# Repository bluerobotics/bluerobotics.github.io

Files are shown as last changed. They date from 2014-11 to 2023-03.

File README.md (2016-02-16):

Blue Robotics Documentation Website 
===================================

This repository is the home to Blue Robotics' product documentation, including product manuals, tutorials, and guides. This information is licensed under the Creative Commons Attribution-ShareAlike 4.0 International License. We welcome and encourage contributions from others as well as reports of issues or errors.

For more information please visit the actual [documentation site](http://docs.bluerobotics.com/).

##How the Website Works

The documentation website uses the [Github Pages feature](https://pages.github.com/) to host the website directly from this repository. The documentation is written in [Markdown](https://help.github.com/articles/markdown-basics/) and uses [Jekyll](http://jekyllrb.com/) to generate the website.

If you want to play around with it and make modifications, just create a [fork of the repository](https://github.com/bluerobotics/bluerobotics.github.io/fork).

When you've got the files on your computer, you can host the site locally by typing:

```bash
jekyll serve
```

Then visit the site at http://localhost:4000/.

For more information on how to install Jekyll on your computer, visit the [Jekyll website](http://jekyllrb.com/).

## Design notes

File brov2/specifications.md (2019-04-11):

---
layout: default
title: BlueROV2
permalink: /brov2/
order: 1
topnavbar: brov2
nav:
- Introduction: introduction
- - Features: features
- - What's Included: whats-included
- - What's Not Included: whats-not-included
- - Resources
- Specifications: specifications
- - Physical: physical
- - Performance: performance
- - Battery: battery
- - Lights: lights
- - Tether: tether
- - Sensors: sensors
- - Camera Tilt: camera-tilt
- - Camera: camera
- 2D Drawing: 2d-drawing
- 3D Model: 3d-model
- User Manuals: user-manuals
- Issue Reporting: issue-reporting

store-links:
- BlueROV2: https://www.bluerobotics.com/store/rov/bluerov2/

manual-links:
- Assembly Manual: /brov2/assembly/
- Software Setup: /brov2/software-setup/
- Operation Manual: /brov2/operation/

redirect: https://bluerobotics.com/store/rov/bluerov2/bluerov2/#tab-technical-details
---

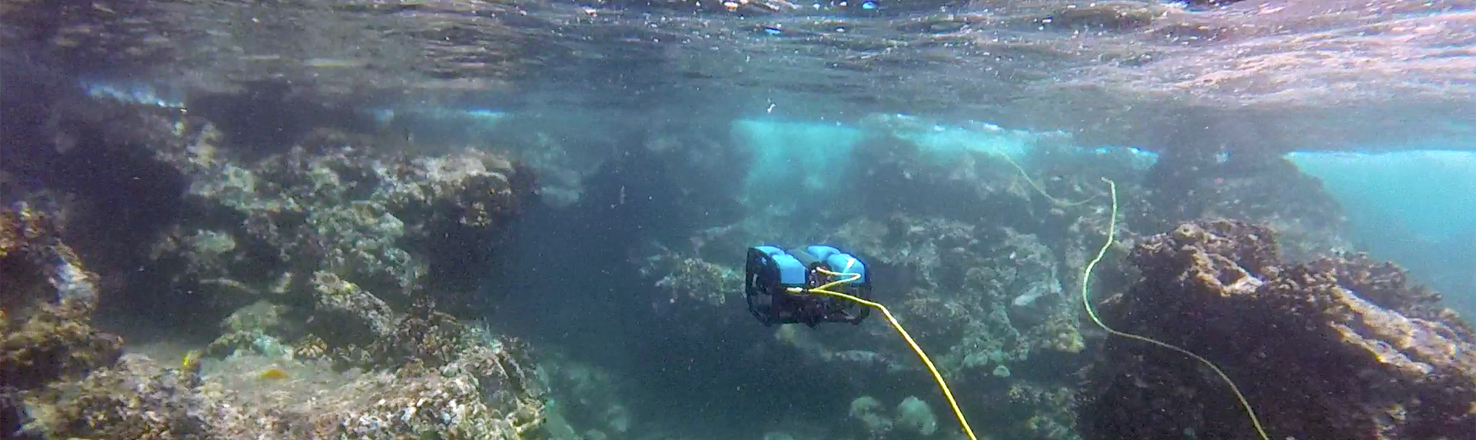
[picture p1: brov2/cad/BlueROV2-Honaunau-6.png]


# Introduction

The _BlueROV2_ is the world's most affordable high-performance ROV. The 6-thruster vectored configuration, coupled with strong static stability, provides a vehicle that is smooth and stable, yet highly maneuverable. The _BlueROV2_ provides the capabilities of a 
high-end commercial mini-ROV at the price of the most basic commercial ROVs.

<a href="http://bluerobotics.com/downloads/bluerov2.pdf" alt="BlueROV2 Datasheet"><i class="fa fa-download" aria-hidden="true"></i> Download Datasheet</a>

## Features

- Live 1080p HD video
- Highly maneuverable vectored thruster configuration
- Stable and optimized for inspection- and research-class missions
- Easy to use, cross-platform user interface
- Highly expandable with three free cable penetrators
- Standard 100m depth rating and up to 300m tether available
- 6 T200 Thrusters and Basic ESCs for the best thrust-to-weight ratio in its class
- Battery powered with quick-swappable batteries for long missions

## What's Included

The kit arrives almost-ready-to-dive with pre-built subassemblies. The expected build time is 1.5-3 hours to operation depending on experience.

You can find the full bill of materials for the for the _BlueROV2_ kit on the [store page](http://www.bluerov2.com/).

## What's Not Included

There are some items necessary for operation that are not included with the kit. 

 - A gamepad controller. We recommend [this XBox One Controller](https://www.microsoft.com/en-us/store/d/xbox-wireless-controller/8vcw8gln9vrf/ljvk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) or [this Logitech Gamepad](http://gaming.logitech.com/en-us/product/f310-gamepad).
 - A laptop or a Windows 10 tablet. QGroundControl works on Mac, Windows 10, and Linux.
 - A battery for the BlueROV2. We recommend getting our [18Ah Lithium-ion Battery](https://www.bluerobotics.com/store/rov/bluerov2/battery-li-4s-18ah-r2-rp/) or 2 or 3 of [these](https://hobbyking.com/en_us/multistar-high-capacity-10000mah-4s-12c-multi-rotor-lipo-pack-w-xt90.html)
 - A battery charger, such as our [Lithium Battery Charger](http://www.bluerobotics.com/store/electronics/batteries/lithium-battery-charger/).  

## Resources

 - [Assembly Instructions](/brov2/assembly/)
 - [Bill of Materials](http://www.bluerov2.com) (see Contents tab)
 - [Initial Software Setup](/brov2/software-setup)
 - [Operating Manual](/brov2/operation)

# Specifications

## Physical 

| Length                                 | 457 mm                     | 18 in                      |
| Width                                  | 338 mm                     | 13.3 in                    |
| Height                                 | 254 mm                     | 10 in                      |
| Weight in Air (with Ballast)           | 10-11 kg                   | 22-24 lb                   |
| Weight in Air (without Ballast)        | 9-10 kg                    | 20-22 lb                   |
| Net Buoyancy (with Ballast)            | 0.2 kg                     | 0.5 lb                     |
| Net Buoyancy (without Ballast)         | 1.4 kg                     | 3 lb                	   |
| Watertight Enclosure Inner Diameter    | 102 mm                     | 4.0 in                     |
| Watertight Enclosure Inner Length      | 298 mm                     | 11.75 in                   |
| Cable Penetrator Holes                 | 14 x 10mm                  | 14 x 0.4 in                |
| Construction                           | HDPE frame, aluminum flanges/end cap, and acrylic tubes |
| Main Tube (Electronics Enclosure)      | [Blue Robotics 4 inch series w/ aluminum end caps](http://docs.bluerobotics.com/watertight-enclosures/#specifications-4-series)        |
| Battery Tube                           | [Blue Robotics 3 inch series w/ aluminum end caps](http://docs.bluerobotics.com/watertight-enclosures/#specifications-3-series)        |
| Buoyancy Foam                          | [R-3318 Urethane Foam](https://www.bluerobotics.com/store/buoyancy-ballast/float-r3318-r1/) rated to 244 meters                |
| Ballast Weight                         | 6 x [200 g coated lead weights](https://www.bluerobotics.com/store/parts/ballast-200g-r1/)                             |
| Battery Connector						 | XT90                                                    |

## Performance 

| Maximum Rated Depth                    | 100 m         | 330 ft        |
| Maximum Tested Depth (so far)          | 130 m         | 425 ft        |
| Maximum Forward Speed                  | 1 m/s         | 2 knots       |
| Thrusters                              | [Blue Robotics T200](http://docs.bluerobotics.com/thrusters/t200/)            |
| ESC                                    | [Blue Robotics Basic 30A ESC](http://docs.bluerobotics.com/besc/)   |
| Thruster Configuration                 | [6 thrusters](http://ardusub.com/images/vectored-frame.png)                   |
|                                        | - 4 Vectored                  | 
|                                        | - 2 Vertical                  | 
| Forward Bollard Thrust (45°)           | 9 kg<sub>f</sub>      | 19.8 lb<sub>f</sub>     |
| Vertical Bollard Thrust                | 7 kg<sub>f</sub>       | 15.4 lb<sub>f</sub>      |
| Lateral Bollard Thrust (45°)           | 9 kg<sub>f</sub>      | 19.8 lb<sub>f</sub>      |

## Battery

| Battery Life (Normal Use)              | ~3 hours w/ [18AH Lithium-ion Battery](https://bluerobotics.com/store/rov/bluerov2/battery-li-4s-18ah-r2-rp/) |
| Battery Life (Light Use)               | ~5 hours w/ [18AH Lithium-ion Battery](https://bluerobotics.com/store/rov/bluerov2/battery-li-4s-18ah-r2-rp/) |

The batteries can be changed in about 30 seconds.

## Lights

| Brightness       | 1500 lumens each with dimming control                  |
| Light Beam Angle | 135 degrees, with adjustable tilt                    |

## Tether

| Diameter | 7.6 mm | 0.30 in |
| Length   | 25-300 m | 80-980 ft |
| Working Strength | 45 kg<sub>f</sub> | 100 lb<sub>f</sub> |
| Breaking Strength | 160 kg<sub>f</sub> | 350 lb<sub>f</sub> |
| Strength Member | Kevlar with waterblock |
| Buoyancy in Freshwater | Neutral |
| Buoyancy in Saltwater | Slightly Positive |
| Conductors | 4 twisted pairs, 26 AWG |

## Sensors

- 3-DOF Gyroscope (on the PixHawk)
- 3-DOF Accelerometer (on the PixHawk)
- 3-DOF Magnetometer (on the PixHawk)
- Internal barometer (on the PixHawk)
- [Blue Robotics Bar 30 Pressure/Depth and Temperature Sensor](http://docs.bluerobotics.com/bar30/) (external) 
- Current and Voltage Sensing (included with the PixHawk)

## Camera Tilt
					   
| Tilt Range                 | +/- 90 degree camera tilt (180 total range)                                             | 
| Tilt Servo                 | Hitec HS-5055MG         |

## Camera

| Field of View (Underwater) | 110 degrees (horizontal)                                                              |                                                      
| Light Sensitivity          | 0.01 [lux](https://en.wikipedia.org/wiki/Lux#Illuminance)                              |
| Resolution                 | 1080p                                                                                 |

## Control System

| Tether Interface Board              	| [Fathom-X Tether Interface Board](http://docs.bluerobotics.com/fathom-x/)                |
| Control System 						| [M Robotics PixHawk](https://www.bluerobotics.com/store/electronics/pixhawk-r1/)         |

# 2D Drawing

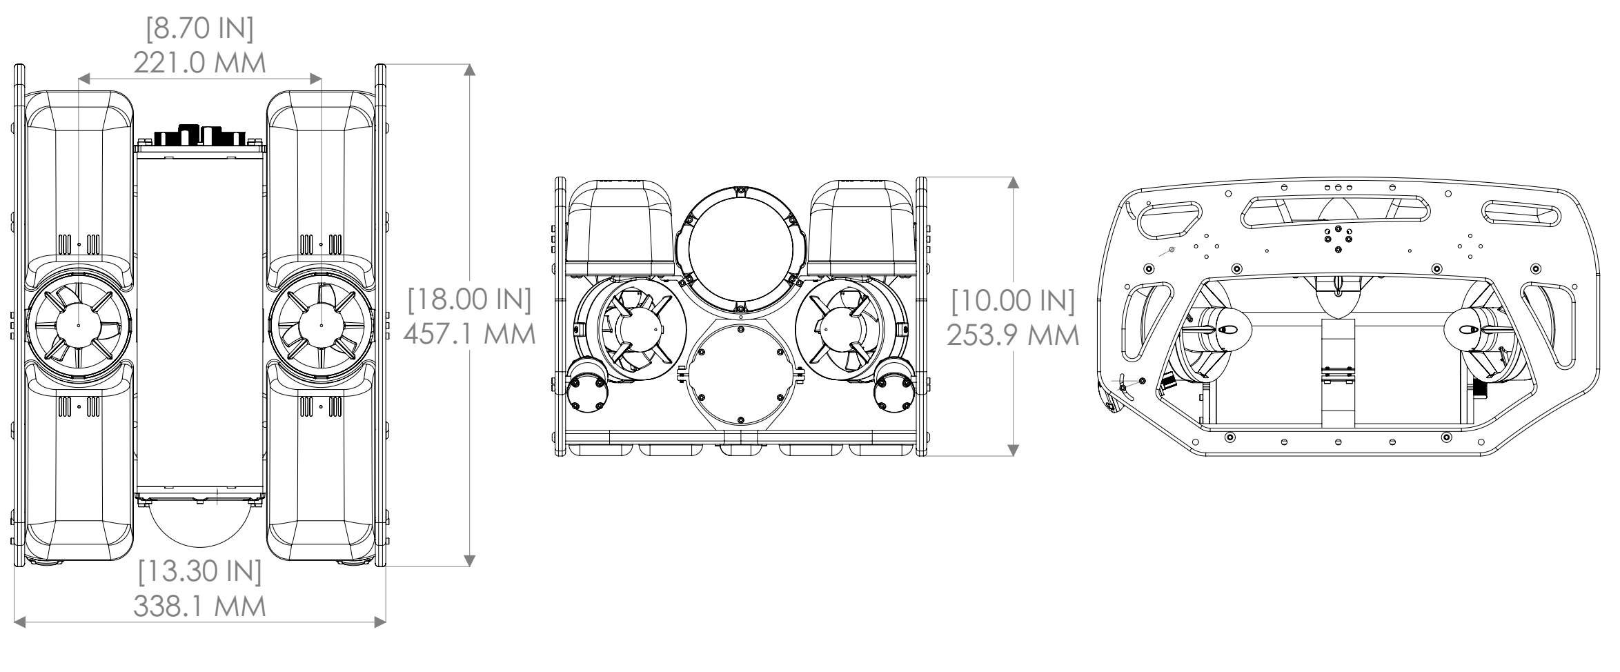
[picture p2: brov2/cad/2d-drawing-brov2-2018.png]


# 3D Model

These are BIG files since the model is fairly complex. If you just want to check out a 3D view or 3D models of the BlueROV, we recommend [checking out the CAD files on GrabCAD](https://grabcad.com/library/bluerobotics-bluerov2-standard-1).

# User Manuals

1. Please look at our [Assembly Manual](/brov2/assembly) for more detailed assembly instructions.

2. If you **received your BlueROV2 after October 24, 2016**, please look at our [Software Setup Manual](/brov2/software-setup/) for more details on setting up your topside computer. If you **received your BlueROV2 prior to October 24, 2016** please look at our [ArduSub Documentation](http://ardusub.com/introduction/#overview) for more details on the control software.

3. Please look at our [_BlueROV2_ Operating Manual](/brov2/operation) for a detailed operating manual.

# Issue Reporting

We're always trying to make our documentation, instructions, software, and user experience better. If you're having an issue with anything, please report it so that we can address it as soon as possible! Here's where to do that depending on what's wrong:

- **ArduSub Issues:** For anything related to the ArduSub software that runs on the Pixhawk and controls the ROV, reports issues on the [ArduSub Github Issues Page](https://github.com/bluerobotics/ardusub/issues). If you're unsure where your issue should be posted, you can report it here.
- **QGroundControl Issues:** For anything related to the QGroundControl software, joystick setup, video streaming, etc., please report an issue on the [QGroundControl Github Issues Page](https://github.com/mavlink/qgroundcontrol/issues).
- **Documentation:** For anything related to the documentation and instructions here, please report an issue on the [Blue Robotics Documentation Github Issues Page](https://github.com/bluerobotics/bluerobotics.github.io/issues).

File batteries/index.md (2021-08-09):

---
layout: default
title: Lithium-Ion Battery Documentation
permalink: /batteries/
order: 1
nav:
- Moved: this-page-has-been-moved

store-links:
- Lithium Battery Charger: http://www.bluerobotics.com/store/electronics/batteries/lithium-battery-charger/
- Lithium-ion Battery (14.8V, 18Ah):  https://www.bluerobotics.com/store/comm-control-power/batteries/battery-li-4s-18ah-r2-rp/
manual-links:
- BlueROV2: /brov2
- Lithium Battery Charger: /charger

redirect: https://bluerobotics.com/learn/battery-info/
---

# This Page Has Been Moved

We're in the process of reorganizing our documentation pages! Most product specifications, 2d drawings, and 3d models have been moved to their respective product pages.

**Please continue to the [Lithium-ion Battery store page on our website](https://www.bluerobotics.com/store/comm-control-power/batteries/battery-li-4s-18ah-r2-rp/) to find the most relevant charger info!**

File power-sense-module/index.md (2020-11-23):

---
layout: default
title: Power Sense Module
permalink: /power-sense-module/
order: 1
nav:
- Installation: installation
- - General: general
- - On the BlueROV2: on-the-bluerov2
- ArduSub Software Setup: ardusub-software-setup

store-links:
- Power Sense Module: https://www.bluerobotics.com/store/sensors-sonars-cameras/sensors/psm-asm-r2-rp-1/

manual-links:
- BlueROV2: /brov2

---

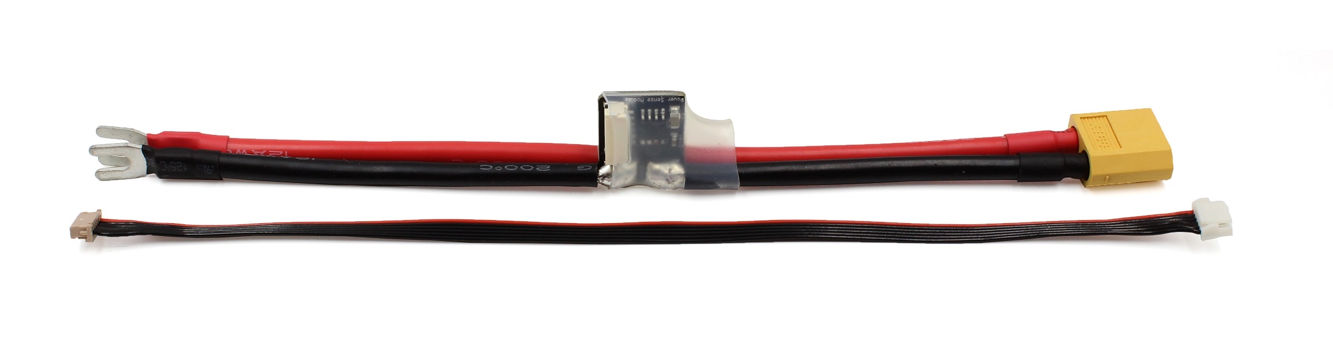
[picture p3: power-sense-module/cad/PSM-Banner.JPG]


# Installation

## General

1. Connect the wires with the attached spades to a power distribution board.
2. Connect the XT60 to a battery or power supply.
3. Connect the 6-position JST-GH to DF13 cable (GH plug side) into the the JST-GH socket on the Power Sense Module.
4. Connect the 6-position JST-GH to DF13 cable (DF13 plug side) into the DF13 POWER socket on the Pixhawk. 

## On the BlueROV2

### Step 1: Remove old Power Module

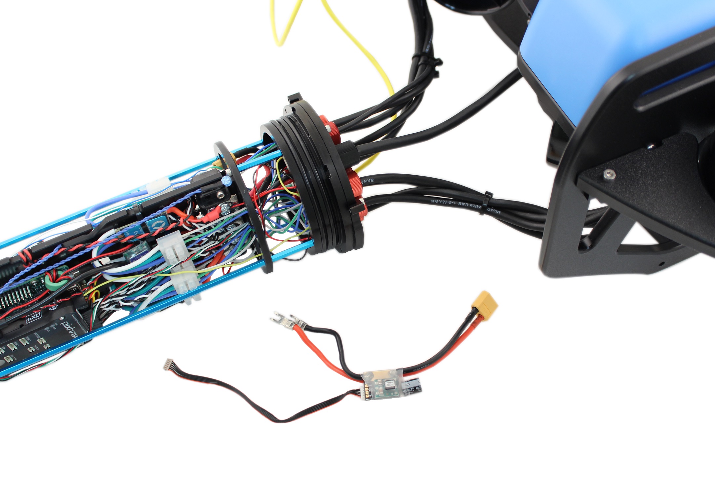
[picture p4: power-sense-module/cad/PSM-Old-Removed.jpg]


Disconnect the old Power Module spade connections (Positive and Negative) on the BlueROV2 terminal blocks. Disconnect the yellow XT60 connector. Depending on when you purchased your ROV, you may have a secondary XT60 connection that can also be disconnected. Disconnect the DF13 cable plug from the POWER port on the Pixhawk.

### Step 2: Connect the power spades

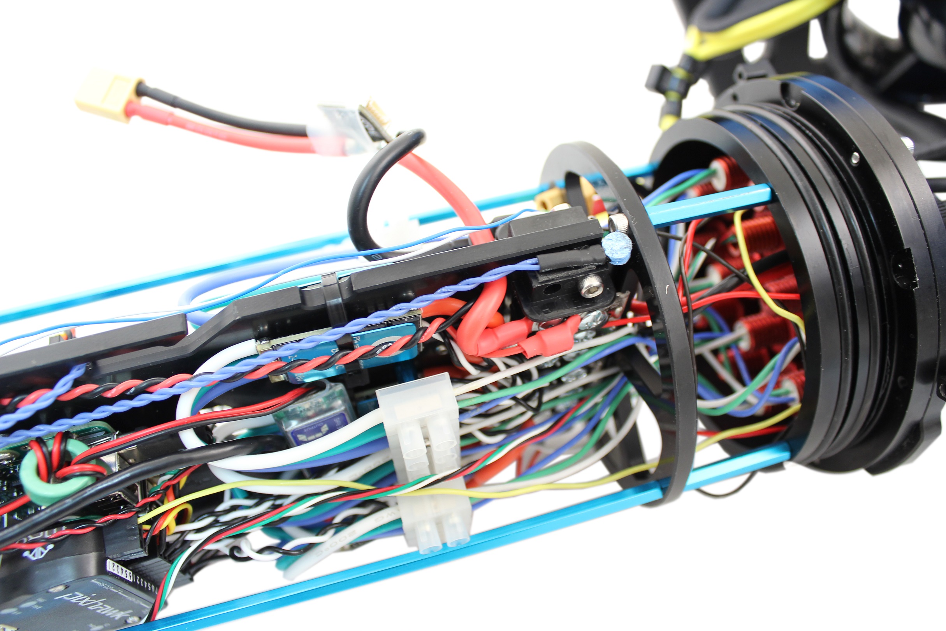
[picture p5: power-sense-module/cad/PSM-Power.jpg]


Connect the positive and negative power wire spades into their respective terminal blocks.

### Step 3: Connect the XT60

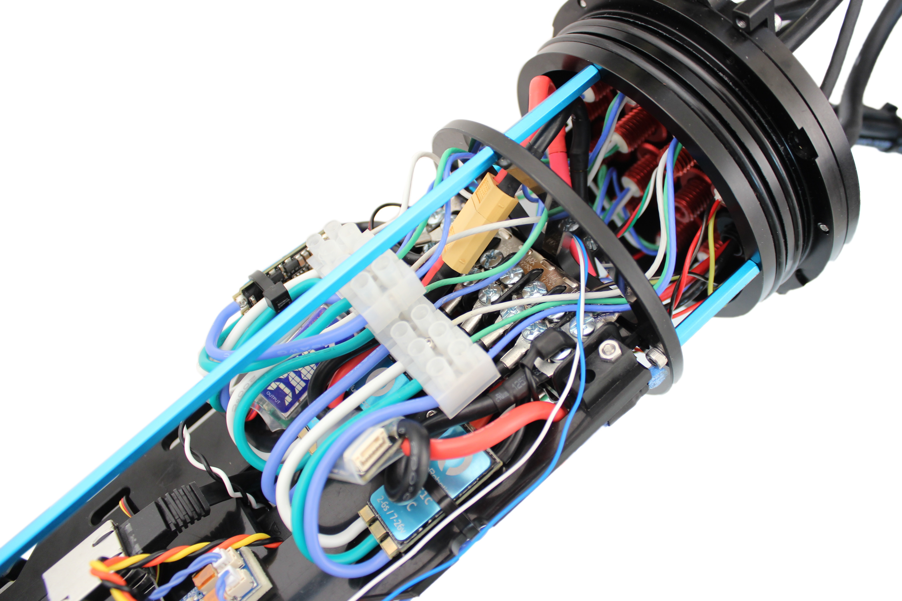
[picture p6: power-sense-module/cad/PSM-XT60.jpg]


Connect the yellow XT60 from the Power Sense Board to the XT60 power input coming from the endcap.

### Step 3: Connect the JST-GH to DF13 cable

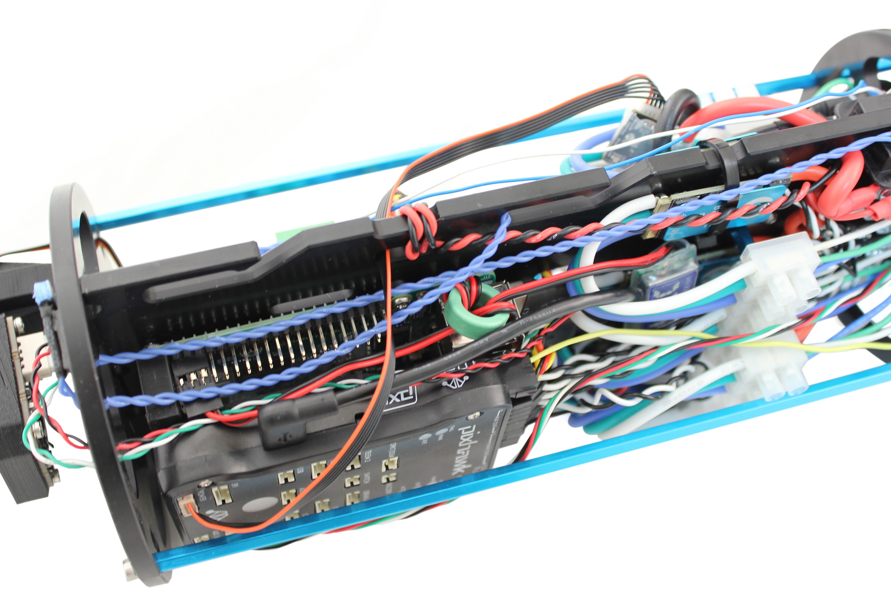
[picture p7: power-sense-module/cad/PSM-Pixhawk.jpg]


Connect the 6-position JST-GH to DF13 cable (GH plug side) into the the JST-GH socket on the <em>Power Sense Module</em>. Connect the JST-GH to DF13 cable (DF13 plug side) into the DF13 POWER socket on the Pixhawk.

# ArduSub Software Setup

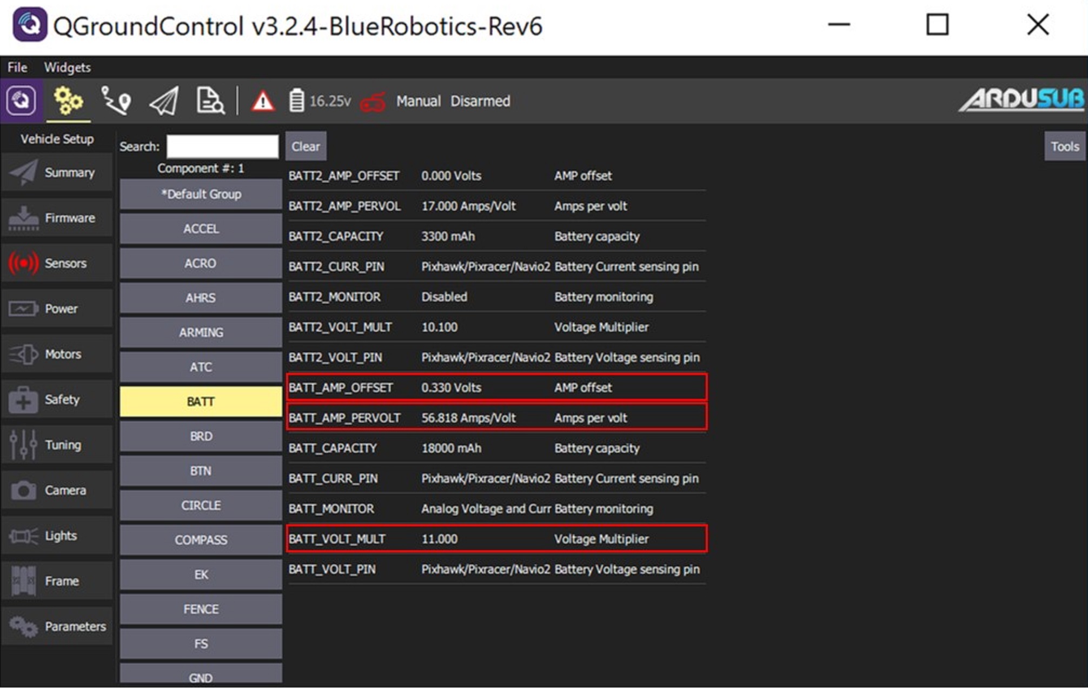
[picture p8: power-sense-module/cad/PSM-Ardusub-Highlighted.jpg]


If you have an R2 PSM (24 mm long):
In the Parameters tab of the QGroundControl Vehicle Setup page, select "BATT" and enter the following values:

| BATT_AMP_OFFSET | 0.330 | Amp Offset | 
| BATT_AMP_PERVOLT | 37.8788 | Amps per volt |
| BATT_VOLT_MULT | 11.000 | Voltage Multiplier |

If you have an R1 PSM (16 mm long):
In the Parameters tab of the QGroundControl Vehicle Setup page, select "BATT" and enter the following values:

| BATT_AMP_OFFSET | 0.330 | Amp Offset | 
| BATT_AMP_PERVOLT | 56.81818 | Amps per volt |
| BATT_VOLT_MULT | 11.000 | Voltage Multiplier |

If you have not already done so, ensure the following values are set:

| BATT_CAPACITY | 18000 | Battery capacity |
| BATT_CURR_PIN | Pixhawk | Battery Current sensing pin |
| BATT_MONITOR | Analog Voltage and Current | Battery monitoring |
| BATT_VOLT_PIN | Pixhawk | Battery Voltage sensing pin |

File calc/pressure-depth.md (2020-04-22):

---
layout: default
title: Pressure/Depth Calculator
permalink: /calc/pressure-depth/
canonical_url: https://bluerobotics.com/learn/pressure-depth-calculator/
order: 0
nav:
- Calculator: calculator
- Learn More: learn-more

redirect: https://bluerobotics.com/learn/pressure-depth-calculator/
---

# Calculator

This calculator determines the water depth to reach or given pressure or the pressure at a given depth. You can enter the depth or pressure input with most common units and it will be converted automatically. This calculator *does not* add air pressure at the surface - the results are relative to the surface pressure.

<div class="well">
<form onsubmit="return false;">
<div class="form-group has-feedback" id="depthInputGroup">
	<label for="depthInput">Input Pressure or Depth</label>
	<input type="text" class="form-control" id="depthInput" placeholder="100 m" onkeyup="checkValidDepth()" aria-describedby="inputSuccess2Status" value="100 m" />
	<span class="glyphicon form-control-feedback" id="depthInputIcon" aria-hidden="true"></span>
  <span id="inputSuccess2Status" class="sr-only">(success)</span>
  <span id="helpBlock" class="help-block">Enter depth or pressure followed by unit. (e.g. "110 psi" or "450 ft")</span>
</div>
<div class="btn-group" data-toggle="buttons">
    <label class="btn btn-primary active">
        <input type="radio" id="freshwater" name="waterType" value="fresh" checked="checked" onchange="checkValidDepth()" /> Freshwater
    </label> 
    <label class="btn btn-primary">
        <input type="radio" id="saltwater" name="waterType" value="salt" onchange="checkValidDepth()"  /> Saltwater
    </label> 
</div>
</form>

<br />

<div class="row">
	<div class="col-sm-6">
		<table class="table table-hover table-condensed">
			<tr>
				<th>Depth</th>
			</tr>
			<tbody id="depthTableContent">
			</tbody>
		</table>
	</div>
	<div class="col-sm-6">
		<table class="table table-hover table-condensed">
			<tr>
				<th>Pressure</th>
			</tr>
			<tbody id="pressureTableContent">
			</tbody>
		</table>
	</div>
</div>

</div>

# Learn More

[See here](http://hyperphysics.phy-astr.gsu.edu/hbase/pflu.html) for an explanation of static fluid pressure.

For watertight enclosure design, please check out [Under Pressure](/resources/#under-pressure-software).

This calculator uses the [js-quantities library](https://github.com/gentooboontoo/js-quantities) by gentooboontoo for unit conversions.

<script type="text/javascript" src="/calc/quantities.js"></script>

<script type="text/javascript" src="/calc/pressure-depth.js"></script>

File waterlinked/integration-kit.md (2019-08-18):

---
layout: default
title: Water Linked Underwater GPS / BlueROV2 Integration Kit Documentation
order: 1
permalink: /waterlinked/integration-kit/
topnavbar: waterlinked
nav:
- Introduction: introduction
- Installation: installation
- - Inside WL Box: inside-wl-box
- - To ROV: to-rov

store-links:
- WL Underwater GPS: http://www.bluerobotics.com/store/electronics/underwater-gps/aps-wl-11001/
- WL Integration Kit: http://www.bluerobotics.com/store/electronics/underwater-gps/aps-wl-brov2-kit-r1/

manual-links:
- Water Linked Underwater GPS: /waterlinked

redirect: https://bluerobotics.com/learn/water-linked-bluerov2-integration-r2-integration-kit/
---

<!--<img src="/switch/cad/switch-4a.png" class="img-responsive" style="max-width:900px"  />-->

# Introduction

The Water Linked Underwater GPS is designed with a generic connection interface so that it can be used in a wide variety of applications, but in its stock configuration, it can be difficult to integrate with the BlueROV2. The *Water Linked Underwater GPS / BlueROV2 Integration Kit* provides a few components to make a seamless connection between the BlueROV2 system and the Water Linked system.

To install the kit on a Water Linked system, you first add a Fathom-X tether interface board to the box so that it can join the BlueROV2's network without an Ethernet switch. We also swap the Ethernet bulkhead on the box for an 8-pin connector that provides a single cable connection between the BlueROV2 topside electronics and the box.

The integration kit requires some minor assembly and instructions are below!

# Installation

## Inside WL Box

Inside the Water Linked box, we'll be adding a Fathom-X tether interface board and a few cables to make integration seamless. This Fathom-X board will be *in addition* to the Fathom-X board that is already used on the ROV topside. The two boards are connected in parallel to the same twisted pair, putting the ROV, topside computer, and Water Linked box on the same computer network.

Here's a diagram of what we'll be connecting inside the box:

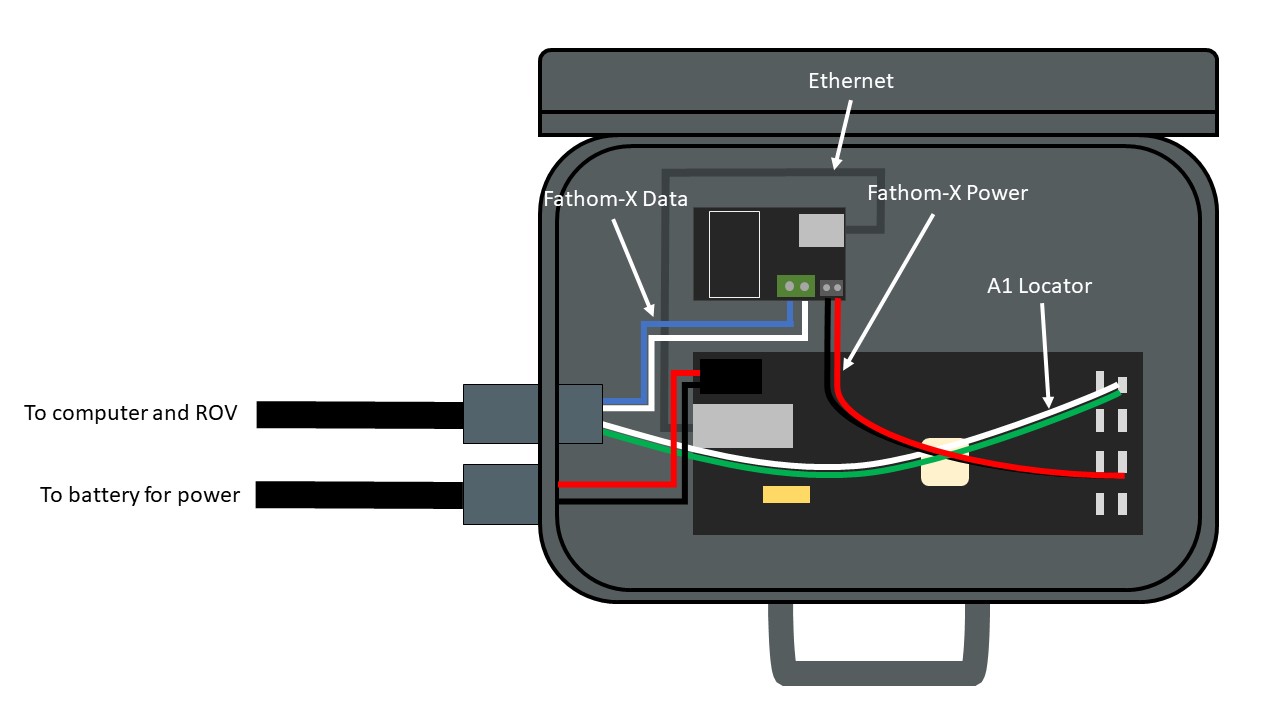
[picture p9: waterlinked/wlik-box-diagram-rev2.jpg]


1. Remove the backing from the red 3M VHB tape on the back of the Fathom-X mount. 
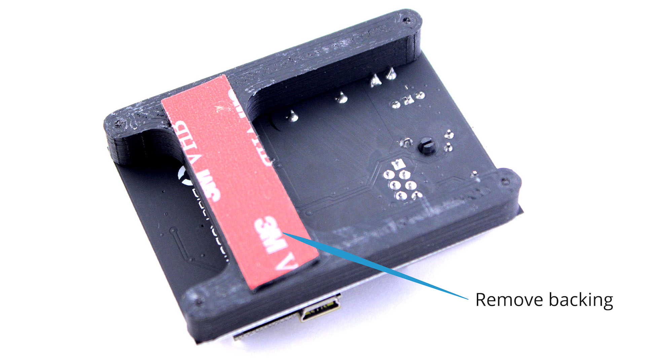
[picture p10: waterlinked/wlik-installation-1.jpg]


2. Install the Fathom-X board in the Water Linked box as shown below.
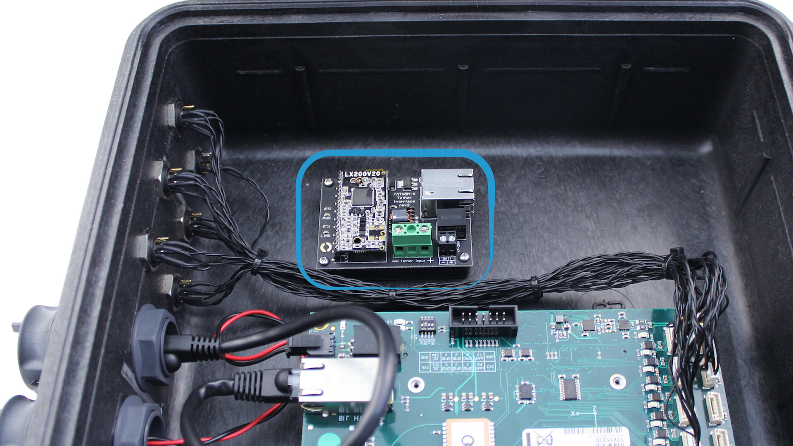
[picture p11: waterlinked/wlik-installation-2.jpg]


3. Unplug the Ethernet cable from the connector on the side of the box, route underneath the Water Linked board, and plug into the Fathom-X module.
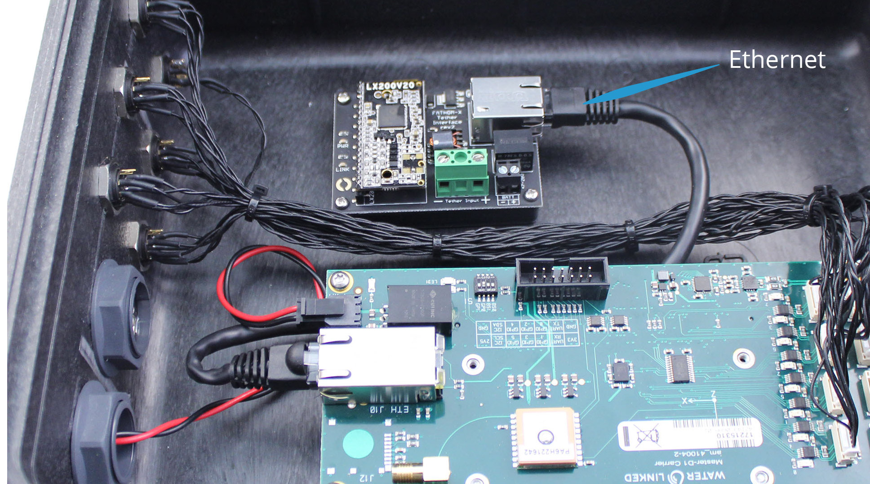
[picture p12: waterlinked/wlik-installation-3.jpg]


4. Remove the Ethernet bulkhead connector from the side of the box. Remove the protective cap from that connector for reuse with the new connector.
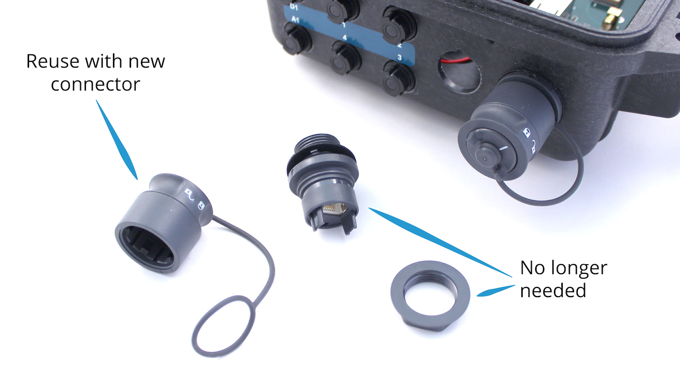
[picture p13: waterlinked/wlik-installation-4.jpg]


5. Install the new bulkhead connector into the same hole, making sure the circle on the connector body is facing upwards. Replace the protective cap.
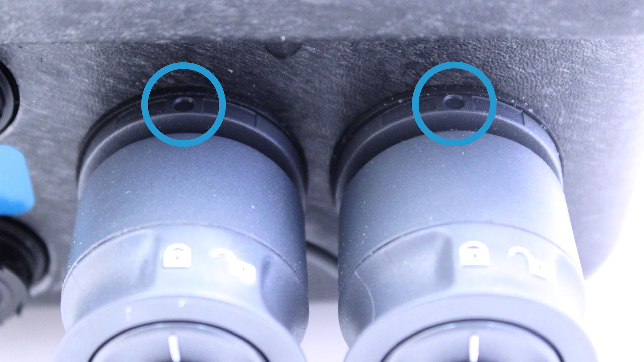
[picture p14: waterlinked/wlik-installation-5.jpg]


6. Using a small flathead screwdriver, connect the red and black wires to the positive and negative tether input terminals on the Fathom-X board.
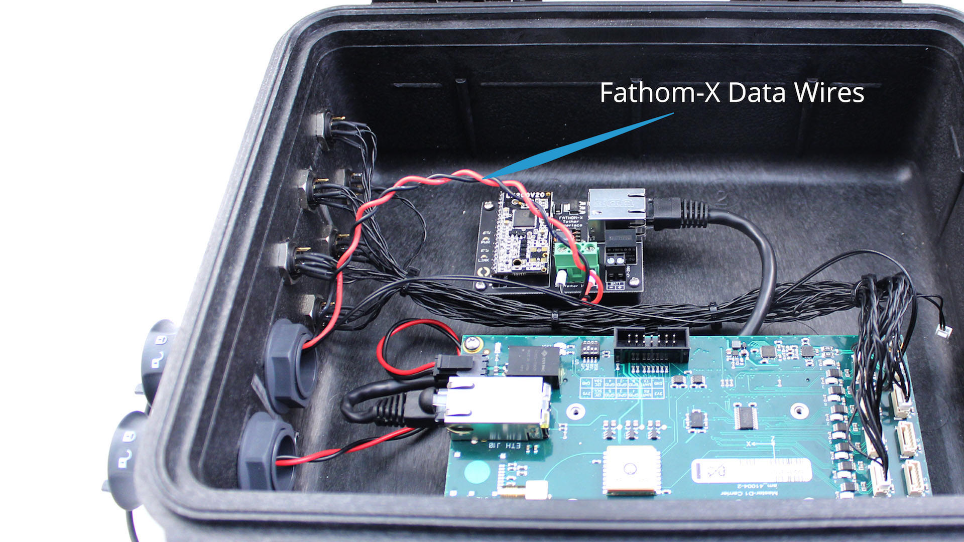
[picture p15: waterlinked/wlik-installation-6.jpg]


7. Next, unplug the small A1 plug from the top right corner of the Water Linked board. Plug in the new A1 plug and leave the original one hanging loose.
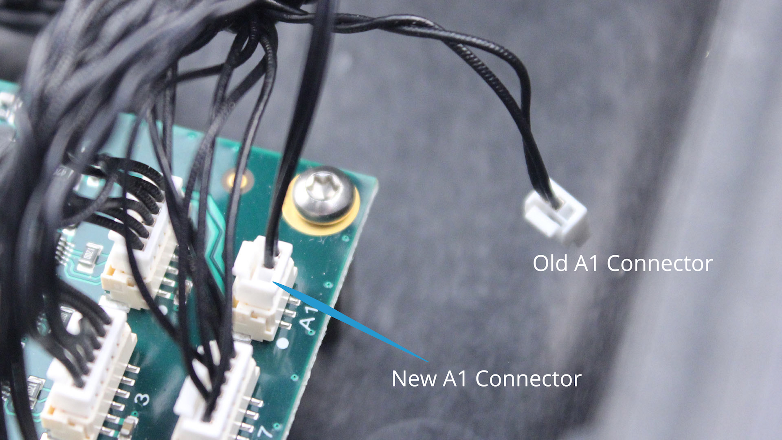
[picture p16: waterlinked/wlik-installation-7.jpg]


8. Plug the Fathom-X power cable into port D5 or D6 on the Water Linked board. Then connect the ferrules on the other ends of those wires to the positive and negative power input on the Fathom-X board (black terminal block).
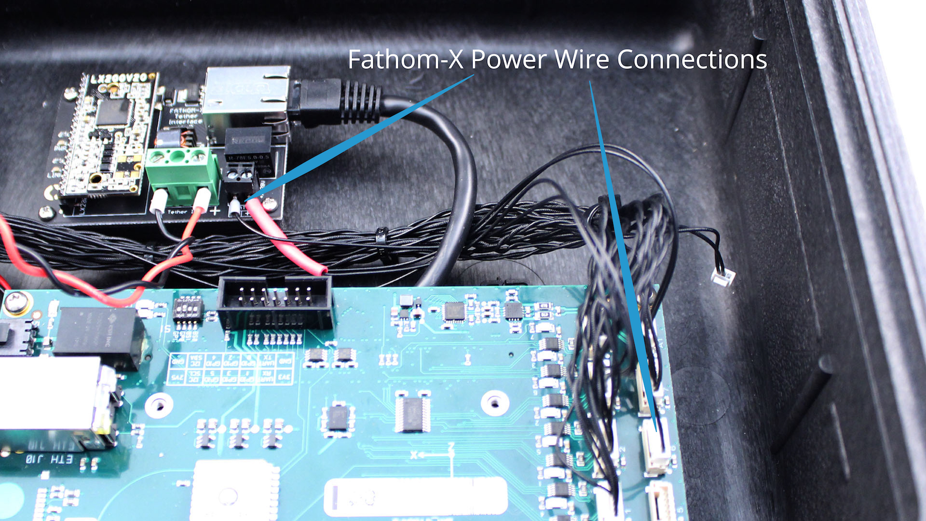
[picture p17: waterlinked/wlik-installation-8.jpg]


9. Add a zip tie to the wiring harness to keep all wires tidy.
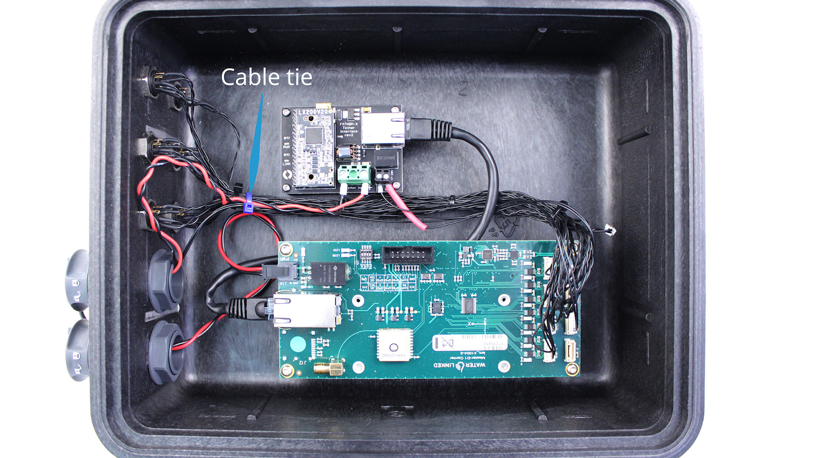
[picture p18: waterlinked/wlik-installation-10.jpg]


Nice job! You're done with modifications to the Water Linked box. Up next, we'll show you how to connect the box to your ROV.

## To ROV
### If using an FXTI (recommended method)
The connections made inside the FXTI will connect the ROV, Topside Computer, and Water Linked systems to each other. Here's a high level diagram of what that will look like:

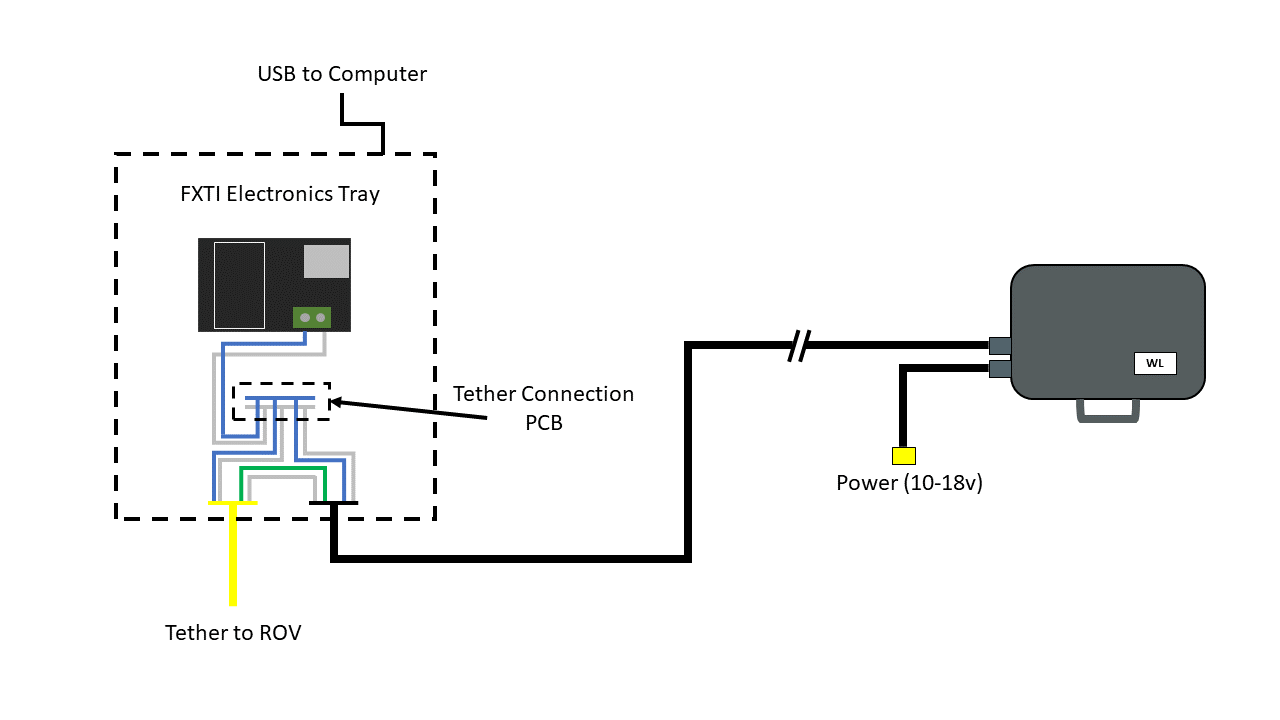
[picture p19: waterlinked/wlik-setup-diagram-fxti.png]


The connections are made on the Tether Connection PCB on the FXTI Electronics Tray and connecting the green Locator-A1 wires. Below is a picture of how the components are connected together along with step by step connection instructions.

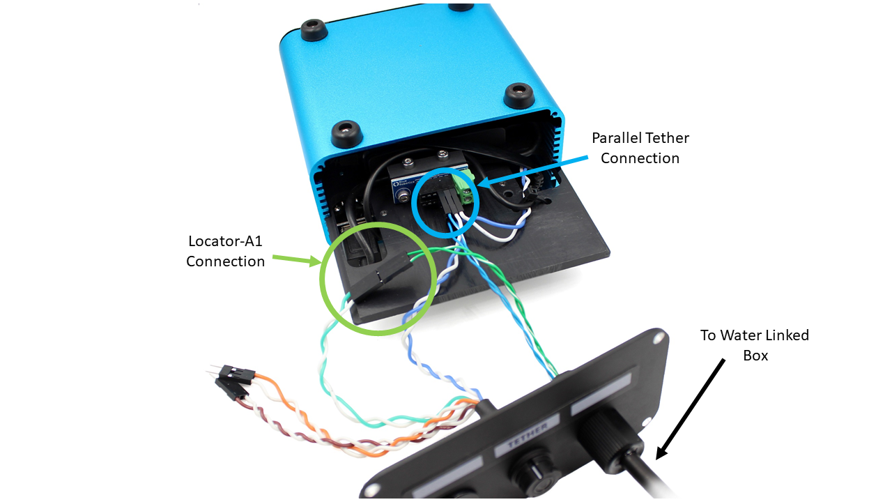
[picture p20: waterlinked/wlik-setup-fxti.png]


1. Remove one of the black plastic FXTI plugs from one of the auxiliary ports.

2. Thread the Water Linked Box to FXTI Cable into the open port and secure in place with the 3D printed spacer and black penetrator nut.

3. Connect the blue and blue/white wire pair into the FXTI Tether Connection PCB matching the orientation of the pre-installed blue and white wire connections.

3. Connect the green and green/white Locator-A1 wire pair into the green and white pair on the Binder connector pigtail, matching colors.

4. Reassemble the FXTI box.

### If using the terminal block and a Fathom-X (depreciated method)
The connections made near the topside Fathom-X interface and topside computer will connect the ROV, Topside Computer, and Water Linked systems to each other. Here's a high level diagram of what that will look like:

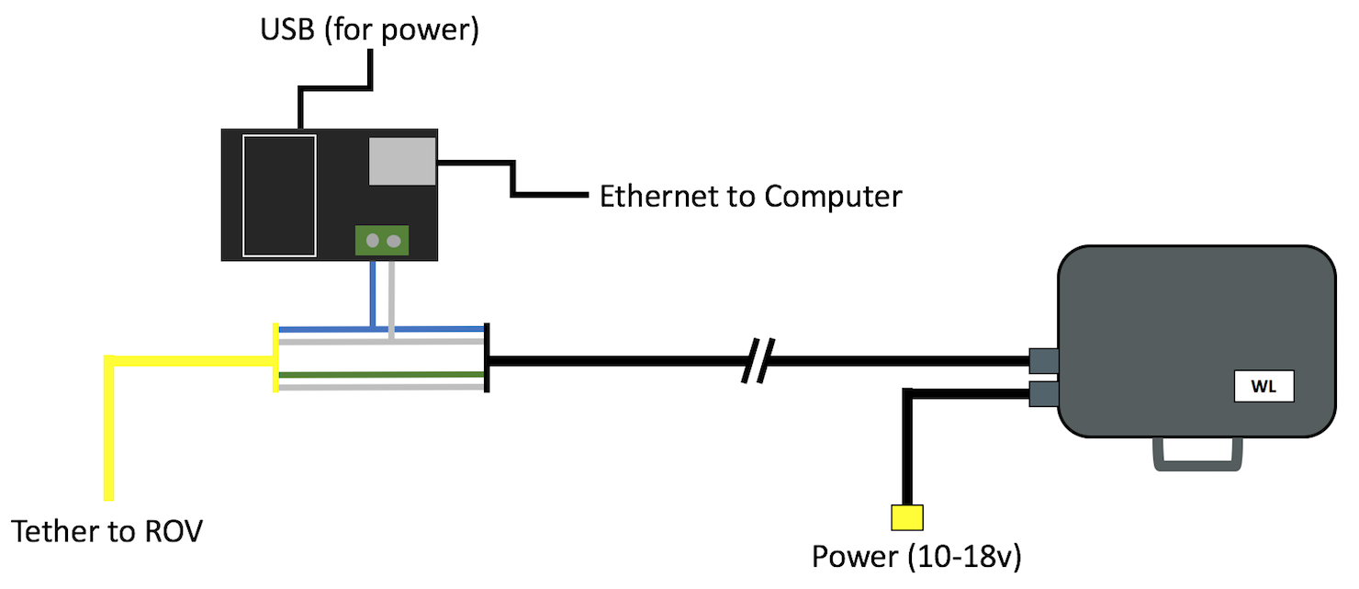
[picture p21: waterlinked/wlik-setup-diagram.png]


These connections are made on a terminal block with a few provided wires. Note that this isn't the nicest solution in the world, using an FXTI as shown above yields a much cleaner installation. Below is a diagram of how the components are connected together along with step by step connection instructions.

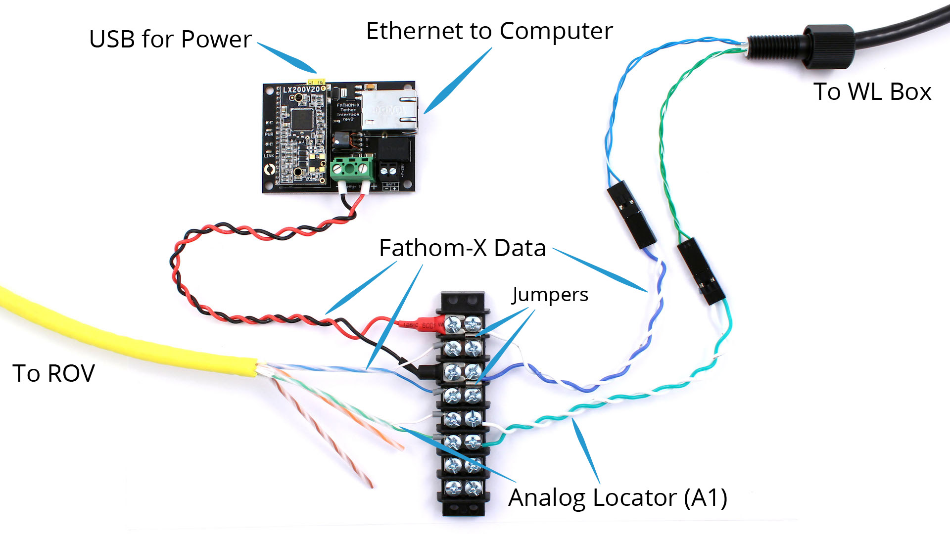
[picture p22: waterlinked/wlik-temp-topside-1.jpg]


1. Connect the red and black wires to the topside Fathom-X board. White and blue heatshrink is used to show the functional connection to the other twisted pairs.

2. Connect the tether blue/white and green/white pairs to the terminal block, matching the existing blue/white and green/white pairs. 

3. Plug the wires from the black Integration Kit cable into the header connectors, matching colors.

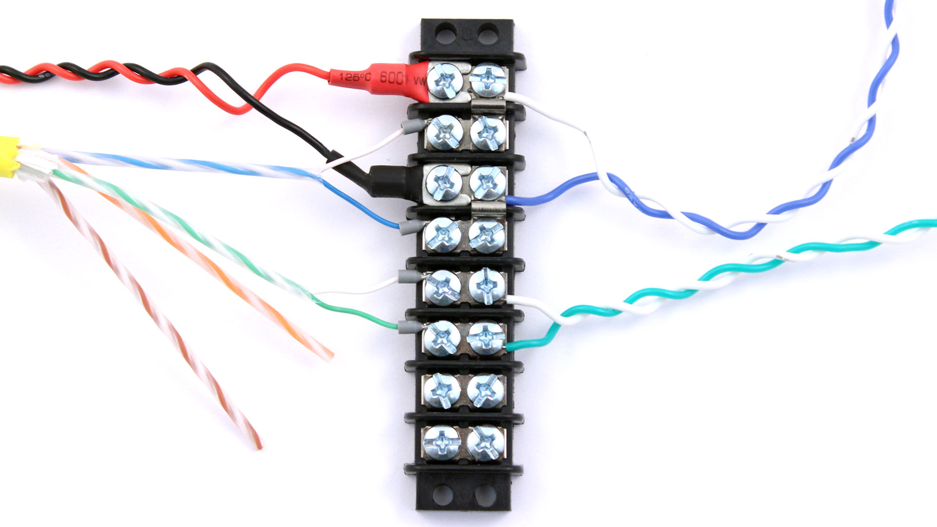
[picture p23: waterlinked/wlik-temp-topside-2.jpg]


**Note:** We strongly recommend mounting the Fathom-X and terminal block in a protective box or case. The wiring here is fairly fragile and easy to damage.

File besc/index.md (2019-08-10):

---
layout: default
title: Basic ESC Documentation (Old)
order: 1
canonical_url: https://bluerobotics.com/store/thrusters/speed-controllers/besc30-r3/
nav:
- Introduction: introduction
- - Safety: safety
- - Quick Start: quick-start
- Specifications: specifications
- - Diagram: diagram
- - Specification Table: specification-table
- - 3D Model: 3d-model
- Installation: installation
- - Thermal Considerations: thermal-considerations
- - Video Tutorial: video-tutorial
- Example Code: example-code
- - Arduino: arduino
- Advanced: advanced
- - Firmware Files: firmware-files
- - Firmware Update and Customization: firmware-update-and-customization

store-links:
- Basic ESC: http://bluerobotics.com/store/speed-controllers/besc-30-r1/

manual-links:
- T100/T200 Thrusters: /thrusters/
- M100 Motor: /thrusters/motors/
---
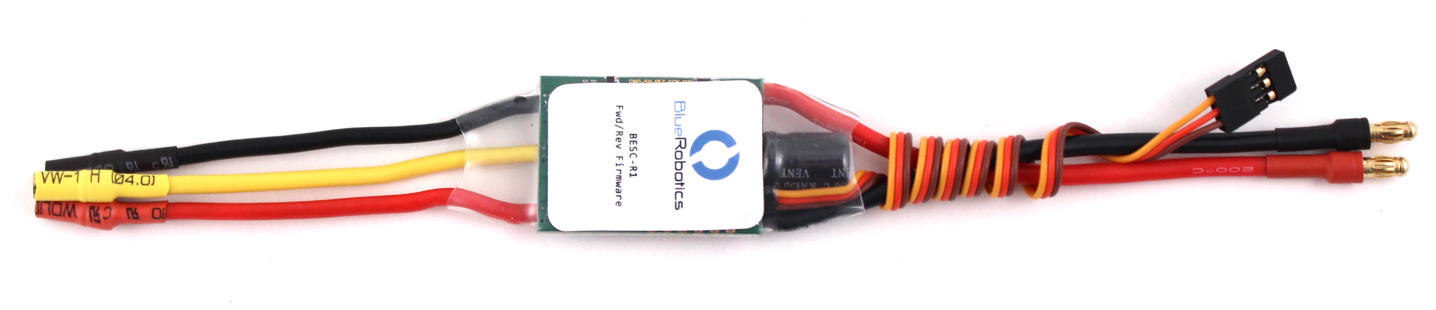
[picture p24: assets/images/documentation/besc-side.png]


# Introduction

NOTE: This is the old version of the BasicESC, the documentation for new R3 version is located [here](http://docs.bluerobotics.com/bescr3/).

The Basic ESC is a simple speed controller. It is the AfroESC 30A pre-programmed with custom firmware that allows forward and backward operation. The firmware is open source and available in [our branch of the tgy project](http://github.com/bluerobotics/tgy).

You are welcome to purchase the ESCs directly and reprogram them yourself. We offer them as a convenience to help you get started quickly. We also do quality control to ensure that every ESC operates correctly. 

Note that the BasicESC no longer includes a BEC, and may only include a signal and ground wire.

## Safety 

<i class="fa fa-exclamation-triangle fa-fw fa-2x text-warning"></i> When working with electricity, especially in water, always practice caution. Always ensure that connections are secure and watertight. Keep your body away from spinning motors and propellers.

## Quick Start

1. Connect the three motor wires to the motor. The order of connections does not matter, however, switching any two wires will change the direction of the motor. The output phases A, B, and C are completely interchangeable
2. Connect the red power wire and black ground wire to a power source like a battery. You will hear a few beeps from the ESC.
3. Connect the signal cable to your signal source like an RC radio receiver or microcontroller board. The yellow wire is the signal wire. The red wire is the battery eliminator circuit (BEC) output, which supplies 5V at 500mA to power a control system (no longer included). The brown wire is ground.
4. Send a stopped signal (1500 microseconds) for a few seconds to initialize the ESC. You will hear a long tone.

# Specifications

## Diagram



## Specification Table

| **Electrical** |
| --- | --- | --- |
| Voltage | 6-16.8 volts |
| Max Current | 30 amps |
| ------------- | ------------- | ------------- |
| **Physical** |
| ------------- | ------------- | ------------- |
| Length | 50 mm | 2.0 in |
| Width | 25 mm | 1.0 in |
| Height | 11 mm | 0.45 in |
| Power Connectors | Male 3.5 mm bullet |
| Motor Connectors | Female 3.5 mm bullet |
| Signal Connector | 3-pin servo connector (0.1" pitch) (ground, 5V, signal) |
| ------------- | ------------- | ------------- |
| **Pulse Width Signal** |
| ------------- | ------------- | ------------- |
| Signal Voltage| 3.3-5 volts |
| Max Update Rate| 400 Hz |
| Stopped | 1500 microseconds |
| Max forward | 1900 microseconds |
| Max reverse | 1100 microseconds |
| Signal Deadband| +/- 25 microseconds (centered around 1500 microseconds) |

## 3D Model

| File Type | Link |
| --- | --- |
| SolidWorks Part (.sldprt)  | [BESC30-R1.sldprt](cad/BESC30-R1.sldprt) |
| STEP (.step) | [BESC30-R1.step](cad/BESC30-R1.step) |
| IGES (.igs) | [BESC30-R1.igs](cad/BESC30-R1.igs) |
| STL (.stl) | [BESC30-R1.stl](cad/BESC30-R1.stl) |

# Installation

## Thermal Considerations

Like all ESCs, the Basic ESC can generate a significant amount of heat when operated. It's important to consider this when mounting and operating the ESC to ensure that it is not damaged by overheating. Most of the heat is generated in the MOSFETs (six black chips about 6mm x 6mm each) and the voltage regulator, which is on the same side of the ESC as the MOSFETs. Here are a few helpful tips:

1.  If possible, make sure the side of the ESC with MOSFETs and voltage regulator is exposed to free air or a heat sink.

2. *Do not* use any adhesives that may insulate the heat generating components, such as silicone sealant.

## Video Tutorial

<iframe width="700" height="393.75" src="https://www.youtube.com/embed/pFAnEkb0Qtg?list=PLZ486nvZoegusCQXQwC-5C-MzKkHBfw0d" frameborder="0" allowfullscreen></iframe>
<br />

# Example Code

## Arduino

This example uses the Arduino Servo library to control the speed controller. This provides an update rate of 50 Hz and can use any pin on the Arduino board as the "servoPin".

If you've never used Arduino before, we suggest checking out [some tutorials!](https://www.arduino.cc/en/Tutorial/HomePage)

**Note:** If you power the Arduino before powering the ESC, then the ESC will miss the initialization step and won't start. Power them up at the same time, power the ESC first, or press "reset" on the Arduino after applying power to the ESC.

~~~~~~~~~~ cpp
#include <Servo.h>

byte servoPin = 9;
Servo servo;

void setup() {
	servo.attach(servoPin);

	servo.writeMicroseconds(1500); // send "stop" signal to ESC.
	delay(1000); // delay to allow the ESC to recognize the stopped signal
}

void loop() {
	int signal = 1700; // Set signal value, which should be between 1100 and 1900

	servo.writeMicroseconds(signal); // Send signal to ESC.
}
~~~~~~~~~~~~~~~~

# Advanced

## Firmware Files

The compiled firmware files can be downloaded here: 

[<i class="fa fa-download fa-fw"></i> Basic ESC Firmware (BESC30-R1)](https://www.bluerobotics.com/downloads/besc30-r1/afro_nfet_besc30_r1.hex)

## Firmware Update and Customization

The Basic ESC uses the [tgy firmware](http://github.com/bluerobotics/tgy) which is open source and editable. There are many parameters that can be changed to change the performance of the speed controller. 

### Firmware Compilation

To compile the firmware, you'll need the avra AVR Assembler.

*Mac:* (Uses Homebrew)

~~~ bash
brew update
brew install avra
make afro_nfet.hex
~~~

### Firmware Flashing

The ESC includes a bootloader that allows flashing through the PWM signal wire using a programming tool like the [Turnigy USB Linker](http://www.hobbyking.com/hobbyking/store/__10628__turnigy_usb_linker_for_aquastar_super_brain.html) or the [AfroESC Programmer](http://www.hobbyking.com/hobbyking/store/__39437__afro_esc_usb_programming_tool.html). 

~~~ bash
avrdude -c stk500v2 -b 9600 -P [programmer port] -p m8 -U flash:w:afro_nfet_besc30_r1.hex:i
~~~

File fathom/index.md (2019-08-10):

---
layout: default
title: Fathom Tether
order: 1
redirect: https://bluerobotics.com/store/cables-connectors/cables/fathom-tether-nb-4p-26awg-r2/
nav:
- Introduction: introduction
- Quick Start 
- Specifications: specifications
- - Specification Table: specification-table
- - Section View: section-view

- Installation: installation
- - Stripping the Jacket: stripping-the-jacket
- - Stripping the Twisted Pairs: stripping-the-twisted-pairs
- - Installing Into a Penetrator: installing-into-a-penetrator

store-links:
- Fathom:  https://www.bluerobotics.com/store/parts/cables/fathom-tether-nb-4p-26awg-r1/
- Thimble:  https://www.bluerobotics.com/store/parts/fathom-p-thimble-r1/
- Penetrator:  https://www.bluerobotics.com/store/parts/penetrator-10-25-a-8mm-r2/
- Potting Kit: https://www.bluerobotics.com/store/tools/tool-potting-kit-r1/
- Loctite Marine Epoxy: https://www.bluerobotics.com/store/tools/loctite-marine-epoxy/

manual-links:
- Watertight Enclosures: /watertight-enclosures
- BlueROV: /bluerov

---


	
# Introduction

The Fathom Tether is a high quality tether cable designed specifically for ROVs and other subsea applications. 
It is neutrally buoyant, has 350+ lb breaking strength, and is embedded with water-blocking fibers to seal any leaks. The tether has a diameter of 7.6mm and is slimmer than the vast majority of comparable ROV tethers.

We put a lot of time into making sure that it has impeccable electrical qualities. The tether carries four unshielded twisted pairs (UTP) of 26AWG wire. 
These pairs are colored and arranged in the same fashion as a Cat5 networking cable including cross-talk resistance. Each pair is individually jacketed inside the cable to maintain reliable properties and minimize interference between each pair of wires.
 
# Quick Start 

1. Prepare the ends of your tether for use as shown in the [installation tutorial](#installation).

2. Be sure to tin the ends of the conductors prior to installing the tether into your vehicle.

3. Firmly attach the tether to your vehicle by following the [strain relief tutorial](/fathom/thimble) or some other method that prevents the tether from pulling directly on the tether penetrator. The tether can twist the penetrator loose if you do not provide strain relief.
 
# Specifications

## Specification Table

| **Physical** |
| --- | --- |
| **Item** | **Value** |
| Tether Diameter | 7.6 mm | 0.30 in |
| Weight | 0.043 kg/m | 0.0287 lbs/ft
| Buoyancy in Freshwater | Neutral 
| Buoyancy in Saltwater | Slightly Positive
| Wire Gauge | 26 AWG |
| Working Strength | 35 kg<sub>f</sub> | 80 lb<sub>f</sub> |
| Breaking Strength | 155 kg<sub>f</sub> | 350 lb<sub>f</sub> |
| Minimum Working Bend Diameter | 200 mm | 8 in |
| ------------- | --------- |

| **Electrical** |
| --- | --- |
| **Item** | **Value** |
| DC Resistance @ 20&deg;C| 0.0386 &Omega; / ft | 0.127 &Omega; / m |
| Characteristic Impedance @ 1 MHz | 120 &Omega; | 
| Capacitance @ 1 kHz | 16.5 pF / kft | 54.1 pF / km |
| Insulation Resistance @ 500 VDC | > 500 M&Omega; / kft | > 1640 M&Omega; / km |
| Voltage Rating (Twisted Pair) | 300 VDC |
| Voltage Rating (Between Pairs)  | 600 VDC |

| **Twisted Pairs** |
|---|---|---|
| **Pair 1** | Wire 1 | White |
| | Wire 2| Blue |
| **Pair 2** | Wire 1 | White |
| | Wire 2 | Orange |
| **Pair 3** | Wire 1 | White |
| | Wire 2 | Green |
| **Pair 4** | Wire 1 | White |
| | Wire 2 | Brown |

## Section View



A datasheet for the polyethylene jacket material is available here: [DF4960 Polyethylene Foam](DF4960.pdf).

# Installation

## Stripping the Jacket

1. Wearing a protective glove, bend the cable at the point that you want to cut. Bending the cable makes it easy to see when you have cut through the jacket.

2. Using a sharp knife, gently slice the jacket open using a sawing motion. Stop when the jacket opens and you can see the white Dacron fibers underneath the jacket.

	

3. Turn the tether over and repeat on the other side.

4. To remove the unneeded part of the jacket, lay the tether on a sturdy flat surface, then cut along the top of the part of the tether that you wish to remove. Take care not to cut deeper than the jacket.

	
	
5. Pull off the length of jacket that you just cut.

	
	
	
	
6. Unwind the clear plastic wrap and white fibers that are wound around the outside of the conductor bundle to the jacket.

	

7. Separate out the white Dacron fibers from the conductor bundle and cut off the all white fibers and plastic wrap at the jacket.

	
	
## Stripping the Twisted Pairs
	
9. Take a jacketed, twisted pair and grab it near the end.

	
	
10. Use a knife to split the pair. Cut into the pair 5 to 10 mm and then you can pull the wires apart using your fingers or pliers.

	
	
11. Cut the excess clear jacket.
	
	
	
12. With the 26 AWG slot on a set of wire strippers, remove the insulation from each conductor.

	
	
13. Tin the ends of the conductors.

	

## Installing into a Penetrator
	
13. Clean the jacket and the tether penetrator that will touch epoxy with isopropyl alcohol.
	
14. Twist the Kevlar and the conductors so that they will slide through the penetrator.

	
	
16. Insert the tether into the penetrator.

	
	
17. Mix a small batch of [Loctite Marine Epoxy](https://www.bluerobotics.com/store/tools/loctite-marine-epoxy/) and pour into a [potting syringe.](https://www.bluerobotics.com/store/tools/tool-potting-kit-r1/)
	
18. Fill the penetrator hole with the epoxy. Move the tether from side to side within the hole to ensure the epoxy is filling all gaps. Use a vice or other secure method to hold the penetrator upright with the tether centered while the epoxy dries.

	
	
19. When the epoxy has dried, apply epoxy to the other side of the penetrator using the same method.

	
	
20. Cut off excess Kevlar strands, and that's it!



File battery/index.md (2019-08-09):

---
layout: default
title: Battery Selection
permalink: /battery/
canonical_url: https://bluerobotics.com/learn/battery-selection-guide-and-calculator/
order: 0
nav:
- Introduction: introduction
- LiPo Batteries: lipo-batteries
- - Voltage: voltage
- - Capacity: capacity
- - Discharge Rate: discharge-rate
- - LiPo Safety: lipo-safety
- - Where to Buy: where-to-buy
- Batteries for the Blue ROV: batteries-for-the-blue-rov
- - Battery Clearance: battery-clearance
- - Example Batteries: example-batteries
- Battery Calculator: battery-calculator
- - Learn More: learn-more

manual-links:
- T100 Thruster: /thrusters/
- T200 Thruster: /thrusters/t200
- Basic ESC: /besc/
- Blue ESC: /bluesc
---

<script type="text/javascript" src="http://cdn.mathjax.org/mathjax/latest/MathJax.js?config=TeX-AMS-MML_HTMLorMML"></script>

# Introduction



The T100 thruster can be powered off of any 6–16V power source, and the T200 off of 6–20V. This can be an AC power supply, lead acid (Pb) battery such as from a car,  nickel metal hydride (NiMH) battery, or a lithium polymer (LiPo) battery. LiPo batteries are particularly light and energy dense while offering high performance with low voltage drop under load, making them the recommended choice for on board ROV power.

# LiPo Batteries



## Voltage

LiPo battery packs come in different voltages, in which each cell is nominally 3.7V.  However, when fully charged a LiPo battery cell rests at 4.2V, and this must be taken into account when determining if your electronics will be able to handle your battery. Furthermore, LiPo batteries should not be discharged below an absolute bare minimum of 3.0V per cell, or permanent damage may occur. Recharging a battery well before this point is reached will ensure good performance and long life of the battery. 

| Battery | Nominal Voltage |  Maximum Voltage |	Recommended Minimum Safe Voltage  (3.4V per cell) |
|---|---|---|---|
| **3s** |  11.1V | 12.6V | 10.2V|
| **4s** | 14.8V | 16.8V | 13.6V|
| **5s**		 | 18.5V | 21.0V | 17.0V|

For maximum efficiency, the T100 should be run at 12V, and the T200 at 16V.  A 11.1V 3s LiPo is recommended for the T100, and a 14.8V 4s LiPo for the T200, though the T100 can be safely run with a 4s pack and the T200 with a 5s pack. If you choose to do this, you will see slightly higher performance, but reduced efficiency than when running at the recommended voltages.

## Capacity

The capacity of a LiPo, or any battery, is in milliamp hours (mAh) or amp hours (Ah) and determines how much energy a battery stores. For example, a 5Ah battery would approximately be able to run a 5 amp device for 1 hour, or a 1 amp device for 5 hours.

## Discharge Rate

The discharge rate is a rating of how much current a battery can safely provide. This is a multiplier of battery capacity, for example a 20C 5Ah battery can safely drive 20 x 5 = 100 amps. Similarly, a 50C 7Ah battery can provide up to 50 x 7 = 350 amps. The burst C rating describes safe maximum current bursts, usually a duration of about 10 seconds. Higher C rated LiPos also have lower voltage drop under load, giving a boost in performance and more punch. 

Running more thrusters off of a single battery will put a greater load on it, so you must use a battery rated high enough such that it will safely be able to power your entire ROV.

| Maximum Current Draw Each | 12V  |  16V	|20V |
|---|---|---|---|
| **T100** |  14.5A | 21.5A | N/A
| **T200** | 18A | 25A | 32A+

## LiPo Safety:

LiPo batteries have a high energy density and must be treated with the proper precautions. More information about LiPo batteries including their correct use and care can be found on the following webpages.

[iCharger (information)](http://www.icharger.co.nz/articles/ArticleId/6/Introduction-To-Lipo-Batteries.aspx)

[iCharger (Safety)](http://www.icharger.co.nz/articles/ArticleId/3/Lipo-Lithium-Battery-Safety-Guide.aspx)

[Horizon Hobby](http://www.horizonhobby.com/pdf/EFL-LiPoSafetyWarnings.pdf)

[Team Orion LiPo Battery Production Video](https://www.youtube.com/watch?v=6vBH6zlrXuM)

## Where to Buy

LiPo batteries can be bought at hobby shops and online through numerous vendors, including [HobbyKing](http://www.hobbyking.com/hobbyking/store/index.asp). We use HobbyKing's Multistar, Turnigy, and Zippy brands of LiPo batteries for our testing.

# Batteries for the Blue ROV

## Battery Clearance

The Blue ROV electronics tray will accommodate batteries up to 230mm (9in) long. However, if basic ESCs are being used, the ESCs mounted to the bottom of the tray will reduce clearances. Past 125mm (4.9in), 5mm (0.2in) of the height available is taken up by the ESC wires. Beyond 155mm (6.1in), 10mm (0.4in) is taken up by the ESC itself.



Due to the round shape of the enclosure, the maximum width of a battery is determined by its height. There is 47.2mm (1.858in) of clearance between the bottom of the electronics tray and the inside of the tube. However, up to an additional 2.5mm (0.098in) of clearance can be found if a battery is squeezed in such that the top shelf of the elctronics tray contacts the tube.

You can use the following formula to determine whether a battery of a given height will fit its width in the enclosure:

$$
\begin{align*}
width=2\times\sqrt{d^2-(h+x)^2}
\end{align*}
$$

Here "d" is the inner diameter of the enclosure, "h" the height of the battery, and "x" the distance the lower part of the electronics tray is from the center of the tube. If "width" is greater than or equal to the width of the battery whose height you input, then the battery will fit, at least in height and width.

$$
\begin{align*}
width=2\times\sqrt{50.8^2-(h+3.6)^2}
\end{align*}
$$

For the Blue ROV, "d" is 50.8mm, and "x" is 3.6mm. If your battery is long enough to come up to the ESC wires or another obstruction on the bottom of the elctronics tray, add its height to "x". Conversely, if you wish to allow the battery tray to be moved up by the battery, you can subtract up to 2.5mm from "x". 

Hobbyking's [battery finder tool](http://www.hobbyking.com/hobbyking/store/multifinder.asp?t=lipo) is very useful in finding batteries that will fit the Blue ROV. Note that the "width" and "height" dimensions in the battery finder tool are the reverse from the variables in the above fit fomula.

## Example Batteries

These batteries will all fit the Blue ROV with basic ESCs, many of them have been used for our testing at Blue Robotics without any issues.

| Battery | Voltage | Capacity | Discharge Rate | Max Constant Current Draw | Cost**|
|---|---|---|---|---|-----|
|[Zippy](http://www.hobbyking.com/hobbyking/store/uh_viewItem.asp?idProduct=63430)  |11.1V (3s)| 6200mAh | 40C |248A| $42
|[Turnigy](http://www.hobbyking.com/hobbyking/store/uh_viewItem.asp?idProduct=11939)|11.1V (3s)| 6000mAh | 25C |150A| $47
|[Turnigy](http://www.hobbyking.com/hobbyking/store/uh_viewItem.asp?idProduct=9184)|11.1V (3s)| 5000mAh | 20C |100A| $22
|[Turnigy](http://www.hobbyking.com/hobbyking/store/__9177__Turnigy_5000mAh_4S_20C_Lipo_Pack.html)|14.8V (4s)| 5000mAh | 20C |100A| $28
|[Zippy](http://hobbyking.com/hobbyking/store/uh_viewItem.asp?idProduct=58781)  |14.8V (4s)| 5000mAh | 30C |150A| $39
|[Multistar](http://www.hobbyking.com/hobbyking/store/uh_viewItem.asp?idProduct=66484)|14.8V (4s)| 6600mAh  | 10C |66A| $43
|[Multistar](http://www.hobbyking.com/hobbyking/store/uh_viewItem.asp?idProduct=66480)*|14.8V (4s)| 10000mAh | 10C |100A| $59
|[Zippy](http://www.hobbyking.com/hobbyking/store/uh_viewItem.asp?idProduct=9959)  |18.5V (5s)| 4000mAh | 40C |160A| $36

*Fits by squeezing electronics tray up, maximum sized battery confirmed to (barely) fit the Blue ROV with basic ESCs.
**Approximate, as of Novemember 2015.

# Battery Calculator 

## (Beta, please double check results & report bugs!)

This calculator finds battery energy based on voltage and capacity ratings. It also estimates how long a battery will run a thruster at a specific throttle level.

<div class="well">
<form>
<div class="form-group has-feedback" id="voltageInputGroup">
	<label for="voltageInput">Nominal Voltage of Battery</label>
	<input type="text" class="form-control" id="voltageInput" onkeyup="runCalcs()" aria-describedby="inputSuccess2Status" value="11.1 V" />
	<span class="glyphicon form-control-feedback" id="voltageInputIcon" aria-hidden="true"></span>
  <span id="inputSuccess2Status" class="sr-only">(success)</span>
  <span id="helpBlock" class="help-block">Enter voltage followed by unit. (e.g. "11.1 V")</span>
</div>

<div class="form-group has-feedback" id="capacityInputGroup">
	<label for="capacityInput">Capacity of Battery</label>
	<input type="text" class="form-control" id="capacityInput" onkeyup="runCalcs()" aria-describedby="inputSuccess2Status" value="5000 mAh" />
	<span class="glyphicon form-control-feedback" id="capacityInputIcon" aria-hidden="true"></span>
  <span id="inputSuccess2Status" class="sr-only">(success)</span>
  <span id="helpBlock" class="help-block">Enter capacity followed by unit. (e.g. "5000 mAh" or "10 Ah")</span>
</div>

</form>

<br />

<div class="row">
	<div class="col-sm-6">
		<table class="table table-hover table-condensed">
			<tr>
				<th>Battery Energy</th>
			</tr>
			<tbody id="energyTableContent">
			</tbody>
		</table>
	</div>
</div>

</div>

## Learn More

This calculator uses the [js-quantities library](https://github.com/gentooboontoo/js-quantities) by gentooboontoo for unit conversions.

<script type="text/javascript" src="/calc/quantities.js"></script>

<script type="text/javascript" src="https://cdnjs.cloudflare.com/ajax/libs/mathjs/2.0.1/math.min.js"></script>

<script src="https://www.google.com/jsapi"></script>

<script type="text/javascript" src="/calc/battery.js"></script>

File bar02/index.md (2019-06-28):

---
layout: default
title: Bar02 Pressure Sensor Documentation
order: 1
nav:
- Installation: installation
- Example Code: example-code
- - Arduino: arduino
- - Python: python

store-links:
- Bar02 Pressure Sensor: https://www.bluerobotics.com/store/electronics/bar02-sensor-r1-rp/
- Celsius Temperature Sensor: https://www.bluerobotics.com/store/electronics/celsius-sensor-r1/
- I2C Level Converter: https://www.bluerobotics.com/store/electronics/level-converter-r1/

manual-links:
- Celsius Temperature Sensor: /celsius
- I2C Level Converter: /level-converter

redirect: https://www.bluerobotics.com/store/sensors-sonars-cameras/sensors/bar02-sensor-r1-rp/
---



# Installation

## Step 1: Lubricating the O-ring

Use a small amount of silicone grease on the O-ring for lubrication and place it in the groove of the Bar02 Pressure Sensor. 

## Step 2: Installation

Install the Bar02 Pressure Sensor into an endcap and tighten by hand or with a wrench.

# Example Code

## Arduino

This example uses the [BlueRobotics MS5837 Library](https://github.com/bluerobotics/BlueRobotics_MS5837_Library) with the connected sensor. The example reads the sensor and prints the resulting values to the serial terminal.

Please remember to use a logic level converter, such as [this one](http://bluerobotics.com/store/electronics/level-converter-r1/), to convert Arduino 5V levels to 3.3V!

If you've never used Arduino before, we suggest checking out [some tutorials](https://www.arduino.cc/en/Tutorial/HomePage)!

~~~~~~~~~~ cpp
#include <Wire.h>
#include "MS5837.h"

MS5837 sensor;

void setup() {
  
  Serial.begin(9600);
  
  Serial.println("Starting");
  
  Wire.begin();

  sensor.setModel(MS5837::MS5837_02BA);
  sensor.init();
  
  sensor.setFluidDensity(997); // kg/m^3 (997 freshwater, 1029 for seawater)
}

void loop() {

  sensor.read();

  Serial.print("Pressure: "); 
  Serial.print(sensor.pressure()); 
  Serial.println(" mbar");
  
  Serial.print("Temperature: "); 
  Serial.print(sensor.temperature()); 
  Serial.println(" deg C");
  
  Serial.print("Depth: "); 
  Serial.print(sensor.depth()); 
  Serial.println(" m");
  
  Serial.print("Altitude: "); 
  Serial.print(sensor.altitude()); 
  Serial.println(" m above mean sea level");

  delay(1000);
}
~~~~~~~~~~~~~~~~

## Python

This example uses the [BlueRobotics MS5837 Python Library](https://github.com/bluerobotics/ms5837-python) with the sensor connected to a Raspberry Pi. The Raspberry Pi uses 3.3V logic levels on the I<sup>2</sup>C pins, so a logic level shifter is not required.

~~~~~~~~~~ cpp
import ms5837
import time

sensor = ms5837.MS5837_02BA() # Default I2C bus is 1 (Raspberry Pi 3)

# We must initialize the sensor before reading it
if not sensor.init():
        print "Sensor could not be initialized"
        exit(1)

# Print readings
while True:
        if sensor.read():
                print("P: %0.1f mbar  %0.3f psi\tT: %0.2f C  %0.2f F") % (
                sensor.pressure(), # Default is mbar (no arguments)
                sensor.pressure(ms5837.UNITS_psi), # Request psi
                sensor.temperature(), # Default is degrees C (no arguments)
                sensor.temperature(ms5837.UNITS_Farenheit)) # Request Farenheit
        else:
                print "Sensor read failed!"
                exit(1)
~~~~~~~~~~~~~~~~

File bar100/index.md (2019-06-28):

---
layout: default
title: Bar100 Pressure Sensor Installation Guide and Sample Code
order: 1
nav:
- Installation: installation
- Example Code: example-code
- - Arduino: arduino
- - Python: python

store-links:
- Bar100 Pressure Sensor: https://www.bluerobotics.com/store/electronics/bar100-sensor-r1/
- Celsius Temperature Sensor: https://www.bluerobotics.com/store/electronics/celsius-sensor-r1/
- I2C Level Converter: https://www.bluerobotics.com/store/electronics/level-converter-r1/

manual-links:
- Celsius Temperature Sensor: /celsius
- I2C Level Converter: /level-converter

redirect: https://www.bluerobotics.com/store/sensors-sonars-cameras/sensors/bar100-sensor-r1/
---



# Installation

## Step 1: Lubricating the O-ring

Use a small amount of silicone grease on the O-ring for lubrication and place it in the groove of the Bar100 Pressure Sensor. 

## Step 2: Installation

Install the Bar100 Pressure Sensor into an endcap and tighten by hand or with a wrench.

# Example Code

## Arduino

This example uses the [BlueRobotics KellerLD Library](https://github.com/bluerobotics/BlueRobotics_KellerLD_Library) with the connected sensor. The example reads the sensor and prints the resulting values to the serial terminal.

Please remember to use a logic level converter, such as [this one](http://www.bluerobotics.com/store/electronics/level-converter-r1/), to convert Arduino 5v levels to 3.3v!

If you've never used Arduino before, we suggest checking out [some tutorials!](https://www.arduino.cc/en/Tutorial/HomePage)

~~~~~~~~~~ cpp
#include <Wire.h>
#include "KellerLD.h"

KellerLD sensor;

void setup() {
  
  Serial.begin(9600);
  
  Serial.println("Starting");
  
  Wire.begin();

  sensor.init();
  sensor.setFluidDensity(997); // kg/m^3 (freshwater, 1029 for seawater)
}

void loop() {
 
  sensor.read();

  Serial.print("Pressure: "); 
  Serial.print(sensor.pressure()); 
  Serial.println(" mbar");
  
  Serial.print("Temperature: "); 
  Serial.print(sensor.temperature()); 
  Serial.println(" deg C");
  
  Serial.print("Depth: "); 
  Serial.print(sensor.depth()); 
  Serial.println(" m");
  
  Serial.print("Altitude: "); 
  Serial.print(sensor.altitude()); 
  Serial.println(" m above mean sea level");

  delay(1000);
}
~~~~~~~~~~~~~~~~

## Python

This example uses the [BlueRobotics KellerLD Python Library](https://github.com/bluerobotics/KellerLD-python) with the sensor connected to a Raspberry Pi. The Raspberry Pi uses 3.3v logic levels on the I2C pins, so a logic level shifter is not required.

~~~~~~~~~~ cpp
from kellerLD import KellerLD
import time

sensor = KellerLD()

if not sensor.init():
  print "Failed to initialize Keller LD sensor!"
  exit(1)

print "Testing Keller LD series pressure sensor"
print "Press Ctrl + C to quit"
time.sleep(3)

while True:
  try:
    sensor.read()
    print("pressure: %7.4f bar\ttemperature: %0.2f C") % (sensor.pressure(), sensor.temperature())
    time.sleep(0.2)
  except Exception as e:
    print e
~~~~~~~~~~~~~~~~

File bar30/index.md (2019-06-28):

---
layout: default
title: Bar30 Pressure Sensor Documentation
order: 1
nav:
- Example Code: example-code
- - Arduino: arduino
- - Python: python

store-links:
- Bar30 Pressure Sensor: https://www.bluerobotics.com/store/electronics/bar30-sensor-r1/
- Celsius Temperature Sensor: https://www.bluerobotics.com/store/electronics/celsius-sensor-r1/
- I2C Level Converter: https://www.bluerobotics.com/store/electronics/level-converter-r1/

manual-links:
- Celsius Temperature Sensor: /celsius
- I2C Level Converter: /level-converter

redirect: https://www.bluerobotics.com/store/sensors-sonars-cameras/sensors/bar30-sensor-r1/
---



# Installation

## Step 1: Lubricating the O-ring

Use a small amount of silicone grease on the O-ring for lubrication and place it in the groove of the Bar30 Pressure Sensor. 

## Step 2: Installation

Install the Bar30 Pressure Sensor into an endcap and tighten by hand or with a wrench.

# Example Code

## Arduino

This example uses the [BlueRobotics MS5837 Library](https://github.com/bluerobotics/BlueRobotics_MS5837_Library) with the connected sensor. The example reads the sensor and prints the resulting values to the serial terminal.

Please remember to use a logic level converter, such as [this one](http://bluerobotics.com/store/electronics/level-converter-r1/), to convert Arduino 5V levels to 3.3V!

If you've never used Arduino before, we suggest checking out [some tutorials!](https://www.arduino.cc/en/Tutorial/HomePage)

~~~~~~~~~~ cpp
#include <Wire.h>
#include "MS5837.h"

MS5837 sensor;

void setup() {
  
  Serial.begin(9600);
  
  Serial.println("Starting");
  
  Wire.begin();

  sensor.init();
  
  sensor.setFluidDensity(997); // kg/m^3 (997 freshwater, 1029 for seawater)
}

void loop() {

  sensor.read();

  Serial.print("Pressure: "); 
  Serial.print(sensor.pressure()); 
  Serial.println(" mbar");
  
  Serial.print("Temperature: "); 
  Serial.print(sensor.temperature()); 
  Serial.println(" deg C");
  
  Serial.print("Depth: "); 
  Serial.print(sensor.depth()); 
  Serial.println(" m");
  
  Serial.print("Altitude: "); 
  Serial.print(sensor.altitude()); 
  Serial.println(" m above mean sea level");

  delay(1000);
}
~~~~~~~~~~~~~~~~

## Python

This example uses the [BlueRobotics MS5837 Python Library](https://github.com/bluerobotics/ms5837-python) with the sensor connected to a Raspberry Pi. The Raspberry Pi uses 3.3V logic levels on the I2C pins, so a logic level shifter is not required.

~~~~~~~~~~ cpp
import ms5837
import time

sensor = ms5837.MS5837_30BA() # Default I2C bus is 1 (Raspberry Pi 3)

# We must initialize the sensor before reading it
if not sensor.init():
        print "Sensor could not be initialized"
        exit(1)

# Print readings
while True:
        if sensor.read():
                print("P: %0.1f mbar  %0.3f psi\tT: %0.2f C  %0.2f F") % (
                sensor.pressure(), # Default is mbar (no arguments)
                sensor.pressure(ms5837.UNITS_psi), # Request psi
                sensor.temperature(), # Default is degrees C (no arguments)
                sensor.temperature(ms5837.UNITS_Farenheit)) # Request Farenheit
        else:
                print "Sensor read failed!"
                exit(1)
~~~~~~~~~~~~~~~~

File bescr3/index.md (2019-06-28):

---
layout: default
title: Basic ESC Documentation (New)
order: 1
nav:
- Example Code: example-code
- - Arduino: arduino
- Advanced: advanced
- - Firmware Files: firmware-files

store-links:
- Basic ESC: https://www.bluerobotics.com/store/electronics/besc30-r3/

manual-links:
- T100/T200 Thrusters: /thrusters/
- M100 Motor: /thrusters/motors/

redirect: https://www.bluerobotics.com/store/thrusters/speed-controllers/besc30-r3/
---
# Example Code

## Arduino

This example uses the Arduino Servo library to control the speed controller. This provides an update rate of 50 Hz and can use any pin on the Arduino board as the "servoPin".

If you've never used Arduino before, we suggest checking out [some tutorials!](https://www.arduino.cc/en/Tutorial/HomePage)

**Note:** If you power the Arduino before powering the ESC, then the ESC will miss the initialization step and won't start. Power them up at the same time, power the ESC first, or press "reset" on the Arduino after applying power to the ESC. You may need to adjust the neutral signal delay time as well, depending on your setup.

~~~~~~~~~~ cpp
#include <Servo.h>

byte servoPin = 9;
Servo servo;

void setup() {
	servo.attach(servoPin);

	servo.writeMicroseconds(1500); // send "stop" signal to ESC.

	delay(7000); // delay to allow the ESC to recognize the stopped signal
}

void loop() {
	int signal = 1700; // Set signal value, which should be between 1100 and 1900

	servo.writeMicroseconds(signal); // Send signal to ESC.
}
~~~~~~~~~~~~~~~~

# Advanced

## Firmware Files

The firmware configuration settings file for BLHeliSuite can be downloaded here: 

[BR Basic ESC BLHEli_S](cad/BLHeli_BR Basic ESC - R_H_15 - Rev. 16.6 - Multi_170921.ini)

Detailed documentation for BlHeli_S operation and settings can be downloaded here:

[BLHeli_S Version 16.x manual](cad/BLHeli_S manual SiLabs Rev16.x.pdf)

## Firmware Update and Customization

The Basic ESC uses version 16.6 of the [BLHeli_S firmware](https://github.com/bitdump/BLHeli/tree/master/BLHeli_S%20SiLabs) which is open source and editable. There are many parameters that can be changed to alter the performance of the speed controller by flashing the ESC through the PWM signal wire using a programming tool like the [Turnigy USB Linker](http://www.hobbyking.com/hobbyking/store/__10628__turnigy_usb_linker_for_aquastar_super_brain.html), the [AfroESC Programmer](http://www.hobbyking.com/hobbyking/store/__39437__afro_esc_usb_programming_tool.html), or an Arduino. The [BLHeliSuite](https://blhelisuite.wordpress.com/) software can be used for accessing the ESC firmware and configuring it.

The Basic ESC uses an SiLabs microcontroller and is Oneshot 125 capable.

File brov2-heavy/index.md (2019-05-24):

---
layout: default
title: BlueROV2 Heavy Retrofit Assembly Tutorial
order: 1
topnavbar: brov2
nav:
- Assembly and Installation: assembly-and-installation
- - Partial Disassembly: bluerov2-partial-disassembly
- - Install New Thrusters: install-new-thrusters
- - Install New Thruster Guards: install-new-thruster-guards
- - Install New Electronics: install-new-electronics
- - Reassemble BlueROV2: reassemble-bluerov2
- - Cable Management: cable-management
- - Install New Buoyancy Blocks: install-new-buoyancy-blocks-and-fairings
- - Mounting Additional Ballast: mounting-additional-ballast-to-the-frame
- Software Setup: software-setup
- - Load New Parameters: load-new-parameters
- - Configure Motor Directions: configure-motor-directions
- - Roll and Pitch Input: roll-and-pitch-input

store-links:
- Heavy Retrofit Kit: https://www.bluerobotics.com/store/rov/bluerov2-upgrade-kits/brov2-heavy-retrofit-r1-rp/

manual-links:
- BlueROV2: /brov2/assembly/
- T200: /thrusters/t200

redirect: https://www.bluerobotics.com/learn/bluerov2-heavy-configuration-retrofit-kit-installation/
---



# Assembly and Installation

## BlueROV2 Partial Disassembly

To partially disassemble your BlueROV2, you will need the following tools:

- 1 x 2.5 mm hex driver
- 1x #1 Phillips head screwdriver
- 1x Wire cutters or scissors
- 1x Penetrator wrench
- Optional: 1x Roll of masking tape and marker

1.	To ensure your ROV is completely powered off, please remove the battery completely from the 3” enclosure and place to the side.

2.	Remove the fairings and buoyancy blocks by removing the self-tapping screws that hold the fairings to the frame.

3.	Optional: In order to ensure thruster mounting is not mixed up, it is recommended to apply short strips of masking tape to the outside of the thruster ducts and labeling them 5,6,7 and 8 respectively according to the thruster diagrams.
    - Thruster 5 (CCW propeller) with red penetrator nut.
    - Thruster 6 (CW propeller) with red penetrator nut.
    - Thruster 7 (CW propeller) with red penetrator nut.
    - Thruster 8 (CCW propeller) with red penetrator nut.    


4.	Remove the M3x12 screws holding Thrusters 5 and 6 to the side panels and place the screws to the side.

5.	Cut and remove any zipties holding the motor wires for Thrusters 5 and 6 to the frame.  

6.	Remove the 4” Electronics enclosure from the ROV by removing the M3x16 screws that mount the enclosure to the ROV cradle.

7. 	Remove the Vent Plug from the Vent Penetrator Bolt on the electronics enclosure.
8.	Remove the Aluminum End Cap with 14 Holes by removing the six M3x12 screws using the M2.5 hex driver. Place the M3x12 screws, clips (small L-shaped parts) in a safe place.

9.	Remove the two blank penetrators as pictured from the 4” End Cap with the penetrator wrench that came with the BlueROV2 kit.


## Install New Thrusters

To Install the new thrusters, you will need the following parts and tools:

-	1 x T200 with counter-clockwise propeller
-	1 x T200 with clockwise propeller
-	1 x Bag with 8 M3x12 screws
-	8 x M3x12 screws you had set aside from removing Thrusters 5 and 6
-	1 x Silicone Grease – 10g Tube
-	1 x Threadlocker
-	1 x Penetrator wrench
-	1 x 2.5 mm hex driver

1.	Install Thrusters 7 and 8 into the respective empty penetrator holes. Tighten to finger tight, then use the provided wrench to tighten them an additional ~1/16 of a turn. If you can’t loosen them with your fingers, they are tight enough.
    - Thruster 7 (CW propeller) with red penetrator nut.
    - Thruster 8 (CCW propeller) with red penetrator nut.    
    

2.	Reinstall the 4” Aluminum End Cap with the following steps:
    - Clean the O-ring and make sure that it is free of any debris or damage.
    - Clean the O-Ring Flange (4” Series) and make sure that the O-ring groove is free of any debris or damage.
    - Apply Silicone grease to the O-ring.
    - Install face seal O-ring onto the O-Ring Flange (4” Series).
    - Apply one drop of threadlocker to each of the M3x12 screws. Roll the screws around on a paper towel to evenly spread the threadlocker and to remove excess threadlocker.
    - Install Aluminum End Cap with 14 Holes with all Cable Penetrators and Blank Penetrators installed onto the O-Ring Flange (4” Series). Do not fully tighten any screws when first installing them; it may cause the O-ring to slip out of its groove. The end cap’s orientation when installed should match the image below. Make sure that the clips are oriented correctly. One should be just right of the Thruster 3 penetrator, and the other should be just left of the Thruster 4 penetrator.
    
<i class="fa fa-exclamation-triangle fa-fw fa-2x text-warning"></i> DO NOT use threadlocker unless you have threadlocker rated for use with polycarbonate.    
    
3.	Install thrusters 5, 6, 7 and 8, using the M3x12 screws on the outside of the side panels. Tighten the screws so that they indent the frame slightly.



## Install New Electronics

To install the new electronics, you will need the following parts and tools:

-	2 x Basic ESC
-	2 x 3 Pole Euro Terminal Block
-	1 x Small (~2 mm) flat head screw driver
-	1 x Large (~#2) Phillips head screw driver

1.	Slide the new 3 pole Euro terminal blocks into their mounting location on top of the 9 pole Euro terminal blocks and one of the poles is between the aluminum standoff.

2.	Connect the motor power wires from the thrusters 7 and 8 to the motor terminal blocks as shown, using your 2 mm flat head screw driver.

3.	Connect the motor power wires from the new ESCs to the motor terminal blocks as shown below, using your 2 mm flat head screw driver.

4.	Plug ESC Signal Wires into Pixhawk with the following steps:
    - Unplug the Lumen light signal wire from the Pixhawk Channel 7 port and replug it into Aux Channel 1 with the yellow wire oriented toward the bottom of the Pixhawk. 
    - Unplug the camera tilt servo from Pixhawk Channel 8 and replug it into Aux Channel 2 with the yellow signal wire oriented toward the bottom of the Pixhawk.
    - Plug the servo signal wire for Thruster 7 into Channel 7 on the Pixhawk with the white signal wire oriented toward the bottom of the Pixhawk.
    - Plug the servo signal wire for Thruster 8 into Channel 8 on the Pixhawk with the white signal wire oriented toward the bottom of the Pixhawk.
5.	Connect the ESC Power Wires into open screw terminals on the respective positive and negative terminal blocks.

6. Secure the ESCs to the tray using one ziptie each and lightly wrapping them around the other ESC motor power wires.


## Install New Thruster Guards

To install the new thruster guards, you will need the following parts and tools:

-	1 Bag of 12 M4x16mm screws
-	1 Bag of #4x3/8” Thread forming screws
-	8 x Heavy Guard Mounting Brackets
-	2 x Heavy Guards
-	1 x Threadlocker
-	1 x #1 Phillips head screwdriver

1. Apply one drop of threadlocker to each of the M4x16mm screws. Roll the screws around on a paper towel to evenly spread the threadlocker and to remove excess threadlocker.
2. Install 4 of the thruster guard mounting brackets on the outside of the frame using 4 M4x16 screws as shown below.

3. Place the new thruster guards on the brackets you had previously installed and make sure the holes align. The thruster guards only install in one direction with the shorter leading edge of the guard oriented towards the front end of the vehicle. If you have Lumen lights mounted in the top mounts, make sure to arrange the wire so it is inside the guard, near the thruster duct. Secure the guards to the brackets using 4 M4x16 screws.

4. Install four more thruster guard mounting brackets (two on each side) in the holes near the middle of the ROV using one M4x16 screw and one #4x3/8” thread forming screw per bracket.

5. Tighten all the screws evenly until they are tight enough to properly secure the thruster guard to the frame and there is no excess freedom of movement.

## Reassemble BlueROV2

To reassemble your BlueROV2, you will need the following parts and tools:

-	4 x M3x16 screws that were placed off to the side during disassembly
-	1 x Silicone Grease – 10g Tube
-	1 x 2.5 mm hex driver

1.	Reinstall 4” Watertight Enclosure onto ROV with the following steps:
    - Apply silicone grease to the two radial O-rings on the O-Ring Flange (4” Series) that is attached to the Electronics Tray then install the Watertight Enclosure (4” Series) with installed Dome End Cap to the O-Ring Flange (4” Series).
    - Mount the Electronics Enclosure to the frame using the M3x16 screws so that the dome is on the same side as the front center panels (the center panels without the 3 large holes). Install the M3x16 screws through the clips and into the Enclosure Cradle (4” Series). It is easier to install these screws if the clips are not fully tightened until all screws are through the clips and threading into the Enclosure Cradle (4” Series). This allows to clips to rotate so you can find the threaded hole in the Enclosure Cradle (4” Series) easily.


## Cable Management

To clean up the thruster and lumen wires, you will need the bag of 30 zip ties and your scissors/wire cutters.

The primary goal of Thruster and Lumen cable management is to prevent the wires from getting cut by the propellers. Make sure to check that no wire can reach a propeller after you have finished routing the cables. Below are some examples of what the cable routing should look like.



## Install New Buoyancy Blocks and Fairings

To install the new buoyancy blocks and fairings, you will need the following parts and tools:

-	16 x Fairing screws that were placed off to the side during disassembly
-	4 x Fairings with buoyancy installed that were placed off to the side during disassembly
-	2 x Heavy additional buoyancy blocks
-	2 x Heavy fairings
-	1 x Bag of 4 fairing screws
-	1 x #1 Phillips head screwdriver
-   1 x #2 Phillips head screwdriver

1.	 Reinstall Original Fairing Blocks onto ROV by installing the screws through the center panels and into the fairings.

2.	Place the new round Heavy buoyancy blocks into the open space where Thrusters 5 and 6 used to be. Ensure the flat sides of the blocks are parallel to the sides of the ROV.

3.	Place the new plastic Heavy fairings on top of the buoyancy blocks and secure them to the old fairing blocks using the included self-tapping fairing screws.




## Mounting Additional Ballast to the Frame

To mount the ballast to the frame you need the following parts and tools:

- 7 x 200g ballast weights (from original BlueROV2 Kit)
- 3 x 200g ballast weights (from Heavy Retrofit Kit)
- 10 x 8-16 Thread, 5/8” Long, Thread-Forming Screws
- 1 x #2 Phillips head screwdriver

To get the longest battery life and the best driving experience, it is important to have the ROV close to balanced from front to back in water and close to neutrally buoyant. The Heavy Retrofit kit adds a bit of weight and more buoyancy to the ROV, so it will need to be retrimmed based on your operating conditions. Trimming the ballast may involve a bit of trial and error. 

# Software Setup

Finally, before operating your ROV, we need to update the software configuration. Begin by powering on your ROV, connecting it to your computer, and opening QGroundControl.

## Load New Parameters

- Go to the _Frame_ tab of the _Vehicle Setup_ page (click the gears icon)
- Click 'Load Vehicle Defaults'
- Click BlueROV2 Heavy. A green bar will move across the top of the screen indicating the progress of loading the parameters; this is usually pretty quick
- **Reboot the vehicle**



## Configure Motor Directions

The motor directions for the BlueROV2 must be configured prior to operation.

<i class="fa fa-exclamation-triangle fa-fw fa-2x text-warning"></i>Be sure to keep all body parts and clothing clear of thrusters while the BlueROV2 is armed.

<i class="fa fa-exclamation-triangle fa-fw fa-2x text-warning"></i>**Do not** run thrusters for longer than 30 seconds in air.

1. Go to the *Vehicle Settings* page in QGroundControl and select the _Motors_ tab in the sidebar on the left.
1. Read and understand the instructions on the setup page
1. Arm the BlueROV2 by clicking the switch on the page
1. One at a time, move each slider, and make sure that the motor that spins is pushing air in the correct direction. If a motor is spinning in the wrong direction, click the corresponding checkbox under the 'Reverse Motor Direction' section to correct the motor rotation.
1. When you are finished with the setup, disarm the ROV by clicking the switch

    

## Roll and Pitch Input

There are currently two methods available for roll and pitch input. 

1. Using the joystick button functions for _trim_roll_ and _trim_pitch_ 

This function is standard with the BlueROV2 setup. 

Push the buttons once, or hold them down to adjust the roll and pitch angle of the vehicle	

	
2. Using the joystick button function _roll_pitch_toggle_ 

This is an advanced function. To setup this function, please reference the [ArduSub Button Setup page](https://www.ardusub.com/getting-started/initial-setup.html#button-setup) (This function is very developmental, use with caution)

Push the button to toggle the function of one joystick between controlling forward/lateral input and controlling roll/pitch input

	
These functions can be assigned to buttons on the joystick in the _Joystick_ tab of the _Vehicle Setup_ menu. The roll and pitch inputs are cleared when switching to MANUAL mode. They are NOT cleared when disarmed.

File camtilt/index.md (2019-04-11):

---
layout: default
title: Camera Tilt System
order: 1
nav:
- This Page Has Moved: this-page-has-moved

store-links:
- Camera Tilt System:  https://bluerobotics.com/store/watertight-enclosures/4-series/camera-tilt-mount/#mount
- Low-Light HD USB Camera: https://bluerobotics.com/store/electronics/cam-usb-low-light-r1/
- Low-Light Analog Camera: https://www.bluerobotics.com/store/electronics/low-light-ntsc-camera/
- Raspberry Pi Camera w/ Wide Angle Lens: https://www.bluerobotics.com/store/electronics/cam-rpi-wide-r1/
- Electronics Tray: https://www.bluerobotics.com/store/watertight-enclosures/4-series/electronics-tray-2/

manual-links:
- Watertight Enclosures: /watertight-enclosures/ 
- Electronics Tray: /etray

redirect: https://www.bluerobotics.com/learn/camera-tilt-system-assembly-guide/
---

# This Page Has Moved

We're glad you ended up here but this page has moved! All of our guides and tutorials are now on our main website at [bluerobotics.com/learn](http://bluerobotics.com/learn/). You can find this particular tutorial [here](https://www.bluerobotics.com/learn/camera-tilt-system-assembly-guide/).

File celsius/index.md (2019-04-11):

---
layout: default
title: Celsius Temperature Sensor Documentation
order: 1
nav:
- Installation: installation
- Example Code: example-code
- - Arduino: arduino

store-links:
- Celsius Temperature Sensor: https://www.bluerobotics.com/store/electronics/celsius-sensor-r1/
- Bar30 Pressure Sensor: https://www.bluerobotics.com/store/electronics/bar30-sensor-r1/
- I2C Level Converter: https://www.bluerobotics.com/store/electronics/level-converter-r1/

manual-links:
- Bar30 Pressure Sensor: /bar30
- I2C Level Converter: /level-converter

redirect: https://www.bluerobotics.com/store/sensors-sonars-cameras/sensors/celsius-sensor-r1/
---



# Installation

## Step 1: Lubricating the O-ring

Use a small amount of silicone grease on the O-ring for lubrication and place it in the groove of the Celsius Temperature Sensor. 

## Step 2: Installation

Install the Celsius Temperature Sensor into an endcap and tighten by hand or with a wrench.

# Example Code

## Arduino

This example uses the [TSYS01 Arduino Library](https://github.com/bluerobotics/BlueRobotics_TSYS01_Library) with the connected sensor. The example reads the sensor and prints the resulting values to the serial terminal.

Please remember to use a logic level converter, such as [this one](http://bluerobotics.com/store/electronics/level-converter-r1/), to convert Arduino 5V levels to 3.3V!

If you've never used Arduino before, we suggest checking out [some tutorials](https://www.arduino.cc/en/Tutorial/HomePage)!

You can find the [TSYS01 Arduino Library](https://github.com/bluerobotics/BlueRobotics_TSYS01_Library) on our [GitHub page.](https://github.com/bluerobotics)

~~~~~~~~~~cpp

#include <Wire.h>
#include "TSYS01.h"

TSYS01 sensor;

void setup() {

  Serial.begin(9600);
  
  Serial.println("Starting");
  
  Wire.begin();

  sensor.init();

}

void loop() {

  sensor.read();
 
  Serial.print("Temperature: ");
  Serial.print(sensor.temperature()); 
  Serial.println(" deg C");
   
  Serial.println("---");

  delay(1000);
}

~~~~~~~~~~~~~~~~

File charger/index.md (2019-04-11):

---
layout: default
title: Lithium Battery Charger Documentation
permalink: /charger/
order: 1
nav:
- Moved: this-page-has-been-moved

store-links:
- Lithium Battery Charger: http://www.bluerobotics.com/store/electronics/batteries/lithium-battery-charger/
- Lithium-ion Battery (14.8V, 18Ah):  https://www.bluerobotics.com/store/comm-control-power/batteries/battery-li-4s-18ah-r2-rp/
manual-links:
- BlueROV2: /brov2
- Lithium-ion Battery (14.8V, 18Ah): /batteries

redirect: https://www.bluerobotics.com/store/comm-control-power/batteries/lithium-battery-charger/
---

# This Page Has Been Moved

We're in the process of reorganizing our documentation pages! Most product specifications, 2d drawings, and 3d models have been moved to their respective product pages.

**Please continue to the [Lithium Battery Charger store page on our website](https://www.bluerobotics.com/store/comm-control-power/batteries/lithium-battery-charger/) to find the most relevant charger info!**

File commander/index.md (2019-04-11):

---
layout: default
title: Thruster Commander
nav:
- Introduction: introduction
- - Why do I need the Thruster Commander?: why-do-i-need-the-thruster-commander
- - Why can't I use the Thruster Commander with other ESCs?: why-cant-i-use-the-thruster-commander-with-other-escs
- - Important Notes: important-notes
- Setup: setup
- - Quick Start: quick-start
- - Modes of Operation: modes-of-operation
- - Powering Thruster Commander: powering-thruster-commander
- - Connecting the Battery and ESCs: connecting-the-battery-and-escs
- - Mounting Thruster Commander: mounting-thruster-commander
- - Enabling Output/Deadman Switch: deadman-switchenabling-output
- - Modifying or Replacing Potentiometers: modifying-or-replacing-potentiometers
- Operation: operation
- - ESC Initialization: esc-initialization
- - Controlling Motors: controlling-motors
- Troubleshooting: troubleshooting

store-links:
- Thruster Commander:  https://www.bluerobotics.com/store/electronics/cmdr-r1-rp/

manual-links:
- Thruster Commander: /commander
- Basic ESC:  /bescr3
- Thrusters: /thrusters

redirect: https://www.bluerobotics.com/store/comm-control-power/elec-packages/cmdr-r1-rp/
---

# Introduction



## Why do I need the _Thruster Commander_?

Most ESCs do not accept simple knob- or button-inputs, instead communicating via pulse-width modulation (PWM) signals.  The _Thruster Commander_ converts up to two potentiometer (knob) inputs to two separate PWM output signals that can be used to control ESCs.  This allows you to run BLDC motors without the need for a complex onboard computer system.

## Why can't I use the _Thruster Commander_ with other ESCs?

Most ESCs are designed for RC airplane or multi-copter use.  Motors on these craft never need to be run in reverse, so most ESCs are uni-directional.  However the _Thruster Commander_ is designed to be used with bi-directional ESCs.  Because of the different operating natures of uni-directional and bi-directional ESCs, the signals required to stop these types of ESCs are different, so the _Thruster Commander_'s safety features (which are meant to stop all attached motors) will not work with uni-directional ESCs. For this reason the _Thruster Commander_ should never be used with uni-directional ESCs.

<i class="fa fa-lightbulb-o fa-fw fa-2x blue"></i>
It is possible to upload bi-directional firmware to some standard ESCs.  More information can be found [in the Basic ESC documentation](http://docs.bluerobotics.com/besc/#firmware-update-and-customization).

## Important Notes

<i class="fa fa-exclamation-triangle fa-fw fa-2x text-warning"></i>
**Only use the _Thruster Commander_ with reversible/bi-directional ESCs** (e.g. [Blue Robotics ESCs](http://docs.bluerobotics.com/besc/#firmware-update-and-customization)).  Standard ESCs are not compatible with the _Thruster Commander_'s safety features.  See [below](#why-cant-i-use-the-thruster-commander-with-other-escs) for more information.

<i class="fa fa-exclamation-triangle fa-fw fa-2x text-warning"></i>
Neither the _Thruster Commander_ nor its included accessories are waterproof.  Make sure to mount them in locations where they will not get wet.

<i class="fa fa-exclamation-triangle fa-fw fa-2x text-warning"></i>
[Deadman switches](#deadman-switchenabling-output) are recommended on any mobile _Thruster Commander_ application.

<i class="fa fa-lightbulb-o fa-fw fa-2x blue"></i>
ESCs are necessary for powering brushless DC (BLDC) motors (e.g. T100 & T200 thrusters), _even to run at full speed_.

<i class="fa fa-lightbulb-o fa-fw fa-2x blue"></i>
Most ESCs require a neutral input signal to [complete their initialization](#esc-initialization).  _This is a safety feature!_  The _Thruster Commander_ will output a neutral signal when:
- SWITCH is open (i.e. not connected to ground),
- input potentiometers are centered, or
- not enough potentiometers are connected.

# Setup

## Quick Start



1. Connect the power cable to the POWER connector in the top left of the board
1. Attach the potentiometer(s) to the inputs (see [Modes of Operation](#modes-of-operation) for input configurations)
    - Each potentiometer’s 3-pin connector can be reversed to reverse its input
1. Attach electronic speed controllers (ESCs) to the output pins
    - The black/brown wire should be connected to the GND pin
    - These connectors should not be reversed
1. Apply 7-28 VDC power to the POWER connector and ESCs
1. To initialize the ESCs, either:
    - Turn the knobs to their center position, or
    - Turn the external switch to the off position
1. That's it! You're ready to go.

### Modes of Operation

| Mode | Inputs | Outputs |
|:---:|:---:|:---:|
| Single Input | SPEED | SPEED <i class="fa fa-arrow-right" aria-hidden="true"></i> Both OUTPUTs |
|  Dual Input  | RIGHT IN and LEFT IN | RIGHT IN <i class="fa fa-arrow-right" aria-hidden="true"></i> RIGHT OUTPUT <br> LEFT IN <i class="fa fa-arrow-right" aria-hidden="true"></i> LEFT OUTPUT |
| Mixed Input  |  SPEED and STEERING  | SPEED and STEERING <i class="fa fa-arrow-right" aria-hidden="true"></i> Both OUTPUTs |
|:------------:|:--------------------:|:-------:|

## Powering _Thruster Commander_

The _Thruster Commander_ can be powered in one of two ways: 7-28 VDC or regulated 5 VDC.  7-28 VDC power can be supplied via the POWER connector in the top left corner of the board.  This can be connected directly to any 7-28 VDC power supply, including the batteries powering your motors.

<i class="fa fa-exclamation-triangle fa-fw fa-2x text-warning"></i>
Make sure the ESCs and motors you are using can handle the voltage you are providing; the _Thruster Commander_ can handle up to 28 volts, but our thrusters cannot: see our [thruster documentation](/thrusters) for more details.

5 VDC regulated power is available from some ESCs with built-in battery eliminator circuits (BECs) which can power the _Thruster Commander_ via the PWM cable, eliminating the need for the 7-28 VDC power input.  These ESCs will have a third, red wire on their PWM input cables which carries the 5 VDC supply.

<i class="fa fa-lightbulb-o fa-fw fa-2x blue"></i>
Note that not all ESCs with such three-wire PWM input cables have built-in BECs.

If none of your ESCs have BECs, you will need to supply either 7-28 VDC power via the POWER connector or 5 VDC regulated power from an external regulator/BEC.  Our Basic ESCs do not have built-in BECs and are not able to power the _Thruster Commander_; they will require the use of the 7-28 VDC power input.

## Connecting the Battery and ESCs

A 6-pole barrier block and jumpers are provided for connecting power between the _Thruster Commander_, ESCs, and the provided XT90 connector/your power source of choice.  The six poles of the barrier block can be connected as shown into two sets of three with the provided jumpers; one set for power (red) and one for ground (black).

<table class="img-center">
    <tr>
        <td style="vertical-align:middle">
            
        </td>
        <td style="vertical-align:middle">
            
        </td>
    </tr>
</table>

The spade connectors from the XT90 connector/power source can be connected beneath two of the jumpers (the spade connectors are too wide to fit on top); this helps to limit the distance the current to the ESCs must flow through the jumpers and barrier blocks.  The _Thruster Commander_ power cable and ESCs can then be connected along the other side of the barrier block.  Note that the _Thruster Commander_ power cable should be omitted if the _Commander_ is being powered via a BEC ([see above](#powering-thruster-commander)).

<i class="fa fa-exclamation-triangle fa-fw fa-2x text-warning"></i>
The _Thruster Commander_, ESCs, and batteries do not contain reverse-polarity or short-circuit protections.  Double-check your wiring before applying power for the first time.

## Mounting _Thruster Commander_

Two M3x0.5 holes spaced 31.75 mm (1.25") apart on the back of each _Thruster Commander_ provide a solid way to mount it on your project.  Alternatively the _Thruster Commander_ can be mounted with double-sided tape.  However you mount the _Thruster Commander_, make sure it is in a location where it will stay dry, because the _Thruster Commander_ and its accessories are **not waterproof**.

The potentiometers can be mounted through a 10 mm (3/8") hole in a panel or box up to 2.5 mm (0.1") thick.  After removing the nut and washer from the potentiometer, pass the potentiometer through the mounting hole from the back of the panel or box.  Replace and tighten the nut and washer, then attach the knobs to the potentiometer by tightening the set screw onto the flat section of the potentiometer shaft using the provided 1.5 mm allen wrench.

## Deadman Switch/Enabling Output

To enable PWM outputs from Thruster Commander, the center SWITCH pin must be connected to ground, indicated on the board as "GND".  This is achieved out-of-the-box with a jumper between the center and GND pins of SWITCH.

A deadman switch can be added by replacing this jumper with any normally-open (NO) momentary switch connected between the center pin and GND.  External "enable" switches can also be used.  Should the switch be released or become disconnected from Thruster Commander, the SWITCH-to-GND connection will be broken and _Thruster Commander_ will stop all connected motors.

<i class="fa fa-exclamation-triangle fa-fw fa-2x text-warning"></i>
If you are using the _Thruster Commander_ on a vehicle, we highly recommend that you install a deadman switch to prevent it from running off without you.

## Modifying or Replacing Potentiometers

The potentiometers included with the _Thruster Commander_ are standard 10 k&Omega; potentiometers with center detents.  These can be replaced with any potentiometers with a resistance of 10 k&Omega; or less.  We recommend those with center detents to make it easier to set the motors to neutral.  To fit the knobs, replacement potentiometers should have 6 mm diameter shafts with flats for a set screw.

Should different-length cables for the potentiometers be necessary, the wires may be lengthened or shortened as desired.  However they should not be run directly alongside wires carrying power for motors, as they may interfere with the potentiometers' analog outputs (i.e. sharing a tether).

# Operation

## ESC Initialization

Most BLDC ESCs have a built-in safety feature that requires a neutral input signal (1500 µs) before they will complete their initialization.  While this reduces the chances of a thruster unexpectedly turning on and lacerating you or your friends, it necessitates an extra initialization step at runtime.

The _Thruster Commander_ outputs a neutral PWM signal to connected ESCs when:
- SWITCH is open (i.e. not connected to ground),
- input potentiometers are centered, or
- not enough potentiometers are connected.

This condition must be held until the ESC gives a high-pitched beep (the fifth beep after being powered on in the case of the Blue Robotics BasicESC).  This beep signifies that the ESC has finished its initialization and is ready to accept an input.

If you are using a deadman switch connected to SWITCH, simply release the button until the ESC beeps to initialize.  Should you be using the included jumper, you will need to center the knobs to initialize the ESCs.

## Controlling Motors

Each _Thruster Commander_ contains two output channels (LEFT OUTPUT and RIGHT OUTPUT) with two sets of output pins each.  This means that the _Thruster Commander_ can control two sets of motors independently.  Three modes of operation are supported: _Single Input_, _Dual Input_, and _Mixed Input_.  The mode is selected by connecting potentiometers to specific inputs.  See [Modes of Operation](#modes-of-operation) for valid combinations of potentiometer connections.

- _Single Input_ uses a single potentiometer connected to the SPEED input to drive both the RIGHT and LEFT OUTPUTs identically.

- _Dual Input_ uses two potentiometer inputs, one on RIGHT IN and one on LEFT IN.  The input on RIGHT IN will dictate the output on RIGHT OUTPUT and the input on LEFT IN will dictate the output on LEFT OUTPUT.

- _Mixed Input_ is designed for use with crafts with left and right thrusters for differential thrust steering.  In these setups, SPEED controls the base speed of the craft and STEERING controls the differential thrust.

The 3-pin connectors on the potentiometers are reversible, so if turning a knob runs the motors the wrong way, the connector can be reversed to correct the problem.  Note that only the potentiometer inputs are reversible; the SWITCH and OUTPUT connectors should not be reversed.  Should you be using a BLDC motor such as the T100 or T200, each motor's direction can be reversed by swapping any two of the three connections between the ESC and the motor.

<i class="fa fa-lightbulb-o fa-fw fa-2x blue"></i>
Potentiometers can be hot-swapped.  However it is advised that this only be done while the outputs are disabled (SWITCH disconnected from GND or power to thrusters disconnected), as hot-swapping potentiometers while the outputs are enabled may cause one or more motors to suddenly start running.

# Troubleshooting

<table>
    <tr>
        <th colspan="2">
            Two short blinks
        </th>
    </tr>
    <tr>
        <td>
            
        </td>
        <td>
            Not enough potentiometers are plugged in.  The <a href="#modes-of-operation">Modes of Operation table</a> shows all valid combinations of potentiometer connections.
        </td>
    </tr>
</table>

<table>
    <tr>
        <th colspan="2">
            One long blink
        </th>
    </tr>
    <tr>
        <td>
            
        </td>
        <td>
            Switch is not pressed/connected, or is not correctly connected.  The SWITCH signal (center) pin must be connected to ground (GND pin) by a switch or jumper for the motors to turn.
        </td>
    </tr>
</table>

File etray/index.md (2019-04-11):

---
layout: default
title: Electronics Tray
order: 1
nav:
- Assembly: assembly
- - Diagram of the Tray: diagram-of-the-tray
- - Assembling the Tray: assembling-the-electronics-tray
- - Installing Terminal Blocks: installing-the-terminal-blocks

store-links:
- Electronics Tray:  https://www.bluerobotics.com/store/watertight-enclosures/4-series/electronics-tray-2/
- Watertight Enclosure for ROV/AUV (4" Series): https://www.bluerobotics.com/store/watertight-enclosures/wte4-asm-r1/
- O-Ring Flange (4" Series): https://www.bluerobotics.com/store/watertight-enclosures/wte4-m-flange-seal-r3/

manual-links:
- Watertight Enclosures: /watertight-enclosures
- Camera Tilt: /camtilt

redirect: https://www.bluerobotics.com/store/watertight-enclosures/4-series/wte4-etray-r1/
---



# Assembly

## Diagram of the Tray

<p align="center">

</p>

## Assembling the Electronics Tray

1. Install the four short standoffs in the four inch O-ring flange. **Do not overtighten. Finger-tight plus 1/8th of a turn will secure these.**

	

2. Install the rear panel on the short standoffs.

	

3. Install the long standoffs into the rear panel.

	

4. Install the main panel and front panel. 

	

5. Now your Etray is ready for installing your electronics.

	

## Installing the Terminal Blocks

The _Electronics Tray_ optionally comes with 2 8-Circuit Barrier Blocks and 2 9-Circuit Eurostyle Terminal Strips, along with their mounting hardware. Below are instructions on how to attach them. Please note that if you are planning on installing [Basic ESCs](https://www.bluerobotics.com/store/speed-controllers/besc-30-r1/), it is easier to install them prior to installing the Barrier/Terminal Blocks. The rest of the electronics that the _Electronics Tray_ is designed for can be mounted easily after the terminal blocks have been installed. 

1. Attach the jumpers to the Black Screw Terminal Block if necessary for your application.

2. Install the 8-Circuit Barrier Blocks onto the main tray.

	

3. Install the standoffs and 9-Circuit Eurostyle Terminal Strip on top of the standoffs.

	

4. Now you are ready to finish installing your electronics!



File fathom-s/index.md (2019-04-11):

---
layout: default
title: Fathom-S Usage Guide
order: 1
nav:
- Installation: installation
- - To Pixhawk: to-pixhawk
- - To Arduino: to-arduino
- - Video Gain Adjustment: video-gain-adjustment
- Advanced: advanced
- - Arduino Programming: arduino-programming
- - Spare Twisted Pair: spare-twisted-pair
- - Connecting Relay or Switch: connecting-relay-or-switch

store-links:
- Fathom-S: https://www.bluerobotics.com/store/electronics/fathom-s-r1/
- Fathom Tether: https://www.bluerobotics.com/store/parts/cables/fathom-tether-nb-4p-26awg-r1/

manual-links:
- Fathom Tether: /fathom/

redirect: https://www.bluerobotics.com/store/comm-control-power/tether-interface/fathom-s-r1/
---



# Installation

## To Pixhawk

To connect to a Pixhawk autopilot, use the DF13 cable included with the Pixhawk to connect the `DF13 UART` connector on the Fathom-S ROV board to the `Telem1` connector on the Pixhawk. Note that you must power the Pixhawk with the Pixhawk power module or another method as the Fathom-S board cannot supply sufficient power.

<a href="/fathom-s/pixhawk-setup.png">Fathom-S and Pixhawk</a>

## To Arduino

To connect to an Arduino, using the header pins on the Fathom-S board and connect the following:

* Fathom-S `RX` to Arduino `RX`
* Fathom-S `TX` to Arduino `TX`
* Fathom-S `5V` to Arduino `5V`
* Fathom-S `GND` to Arduino `GND`

<a href="/fathom-s/arduino-setup.png">Fathom-S and Arduino</a>

## Video Gain Adjustment

The video gain potentiometer allows the video receiver gain to be adjusted for different tether lengths. This makes a relatively minor difference in video quality but is noticeable over widely different lengths.

<a href="/fathom-s/Fathom-S-Gain.png">Fathom-S Gain Potentiometer</a>

The potentiometer can be adjusted for gain suitable for 10m length to 700m length.

# Advanced

## Arduino Programming

The *Fathom-S* board includes features to allow an Arduino microcontroller to be programmed through a tether. To enable that feature:

1. Install the `RTS RESET JMPR` on the topside board

2. Make sure the ROV board has a jumper installed for `TETHER PWR-SW`

3. Connect the Arduino serial port to the tether board via the `GND`, `+5V`, `RX`, and `TX` pins. Make sure the Arduino is *only* powered via the tether board. This is required so that it will reset when the tether board resets.

4. Select the appropriate serial port in the Arduino IDE and program like normal!

## Spare Twisted Pair

In some applications, an addition twisted pair may be needed from the tether for other devices. In this case, you can disconnect Pair 4 from the tether boards and use it for other applications. This will disable the power-on feature so `ALWAYS ON` jumper must be installed.

## Connecting Relay or Switch

The *Fathom-S* board includes logic to turn itself on through the tether connection. This can also be used to turn on an entire ROV by powering a relay or MOSFET switch. The `SW` pins provide a switched battery connection for this purpose.

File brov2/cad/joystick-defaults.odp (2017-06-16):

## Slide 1

Increase Gain

[Trim Pitch Forward]

Decrease Gain

[Trim Pitch Backward]

Camera Tilt Down

Camera Tilt Up


Disarm

Arm

Shift

Stabilize Mode

Depth Hold Mode

Manual Mode

Lights Up

[Trim Roll Left]

Lights Down

[Trim Roll Right]

Forward

Ascend

Lateral

Left

Lateral

Right

Yaw

Left

Yaw

Right

Camera Tilt Center

(Push Joystick In)

Toggle Input Hold

(Push Joystick In)

Reverse

Descend

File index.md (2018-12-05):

---
layout: default
title: Documentation
order: 0
nav:
- How to Contribute: how-to-contribute
- License: license
---

# We're working on improving our documentation.

<p class="lead">Our product info can now be found in the <strong>Technical Details</strong> and <strong>Learn</strong> tabs on each product store page.</p>



You can [contribute, point out errors, and make suggestions](#how-to-contribute) to help us improve the documentation.

# How to Contribute

Want to help us improve our documentation? There are several way to help out.

This page is hosted by and version-controlled through Github.com. Check out the repository here: [github.com/bluerobotics/bluerobotics.github.io](http://github.com/bluerobotics/bluerobotics.github.io).

* **Issues.** You can submit issues like errors, missing content, etc. via Github's issue reporting tools

* **Contribution.** If you are interested in writing larger sections of documentation including new pages, tutorials, etc. you should make a [fork](https://github.com/bluerobotics/bluerobotics.github.io) of this repository, write your content, and then ask us to [pull](https://github.com/bluerobotics/bluerobotics.github.io/pulls) that content into the main repository.

[Here is an example page](/example/) showing what formatting is possible using the Markdown text format.

[Here is a short tutorial](/jekyll-tutorial/) showing how to edit the documentation locally and push changes to your fork.

**The current build status of the documentation is:**



# License

[](http://creativecommons.org/licenses/by-sa/4.0/)

The Blue Robotics Documentation is licensed under a [Creative Commons Attribution-ShareAlike 4.0 International License](http://creativecommons.org/licenses/by-sa/4.0/).

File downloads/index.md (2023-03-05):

---
layout: default
title: Downloads
order: 1
nav:
- Introduction: introduction
---

# Introduction

Here you will find links for all of the software components you will need to operate an ROV like the BlueROV2. For more information on how to use this software to operate an ROV, please visit [ardusub.com](https://www.ardusub.com).

## QGroundControl

- [Windows](https://s3.amazonaws.com/downloads.bluerobotics.com/QGC/latest/QGroundControl-installer.exe)
- [Mac](https://s3.amazonaws.com/downloads.bluerobotics.com/QGC/latest/QGroundControl.dmg)
- [Linux](https://s3.amazonaws.com/downloads.bluerobotics.com/QGC/latest/QGroundControl.AppImage)

Previous releases of QGroundControl can be found on our [github releases](https://github.com/bluerobotics/qgroundcontrol/releases) page.

## ArduSub Firmware Files

**Stable Release for Pixhawk (Pixhawk1):** <i class="fa fa-download" aria-hidden="true"></i> [ArduSub V4.0](https://firmware.ardupilot.org/Sub/stable-4.0.1/Pixhawk1/ardusub.apj)

Firmware for other platforms can be downloaded from [firmware.ardupilot.org](https://firmware.ardupilot.org/). See [here](https://www.ardusub.com/getting-started/installation.html#ardusub) for instructions on how to flash the Pixhawk.

## Raspberry Pi Images

This is a fully configured image for the Raspberry Pi 3 computer to be used as a *companion computer* for the Pixhawk autopilot running ArduSub. See [here](https://www.ardusub.com/getting-started/installation.html#raspberry-pi) for instructions on how to flash the image to the SD card.

<i class="fa fa-download" aria-hidden="true"></i> [Latest Ardusub-Raspbian Image](https://s3.amazonaws.com/downloads.bluerobotics.com/Pi/stable/ardusub-raspbian.img.zip)

## Parameter Files

**[BlueROV2 heavy configuration default parameters](brov2-heavy-3_5_2.params)**

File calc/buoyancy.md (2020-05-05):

---
layout: default
title: Buoyancy Calculator
permalink: /calc/buoyancy/
canonical_url: https://bluerobotics.com/learn/buoyancy-calculator/
order: 0
nav:
- Calculator: calculator
- Densities of Common Materials: densities-of-common-materials
- Learn More: learn-more

redirect: https://bluerobotics.com/learn/buoyancy-calculator/
---

# Calculator 

# (Beta, please double check results & report bugs!)

This calculator finds the buoyancy of an object based on it's displacement. It also uses the object weight or density to find the net buoyancy.

<div class="well">
<form>
<div class="form-group has-feedback" id="volumeInputGroup">
	<label for="volumeInput">Displacement of Object</label>
	<input type="text" class="form-control" id="volumeInput" onkeyup="runCalcs()" aria-describedby="inputSuccess2Status" value="50 in^3" />
	<span class="glyphicon form-control-feedback" id="volumeInputIcon" aria-hidden="true"></span>
  <span id="inputSuccess2Status" class="sr-only">(success)</span>
  <span id="helpBlock" class="help-block">Enter volume followed by unit. (e.g. "0.1 m^3" or "20 in^3")</span>
</div>

<div class="form-group has-feedback" id="weightInputGroup">
	<label for="weightInput">Object Weight, Mass, or Density</label>
	<input type="text" class="form-control" id="weightInput" onkeyup="runCalcs()" aria-describedby="inputSuccess2Status" value="12 lb/ft^3" />
	<span class="glyphicon form-control-feedback" id="weightInputIcon" aria-hidden="true"></span>
  <span id="inputSuccess2Status" class="sr-only">(success)</span>
  <span id="helpBlock" class="help-block">Enter weight or density followed by unit. (e.g. "2.1 kg" or "12 lb/ft^3")</span>
</div>

<div class="btn-group" data-toggle="buttons">
    <label class="btn btn-primary active">
        <input type="radio" id="freshwater" name="waterType" value="fresh" checked="checked" onchange="runCalcs()" /> Freshwater
    </label> 
    <label class="btn btn-primary">
        <input type="radio" id="saltwater" name="waterType" value="salt" onchange="runCalcs()"  /> Saltwater
    </label> 
</div>
</form>

<br />

<div class="row">
	<div class="col-sm-6">
		<table class="table table-hover table-condensed">
			<tr>
				<th>Net Buoyancy</th>
			</tr>
			<tbody id="netBuoyancyTableContent">
			</tbody>
		</table>
	</div>
	<div class="col-sm-6">
		<table class="table table-hover table-condensed">
			<tr>
				<th>Buoyancy</th>
			</tr>
			<tbody id="buoyancyTableContent">
			</tbody>
		</table>
	</div>
</div>

<div class="row">
	<div class="col-sm-6">
		<table class="table table-hover table-condensed">
			<tr>
				<th>Weight</th>
			</tr>
			<tbody id="weightTableContent">
			</tbody>
		</table>
	</div>
	<div class="col-sm-6">
		<table class="table table-hover table-condensed">
			<tr>
				<th>Average Density</th>
			</tr>
			<tbody id="densityTableContent">
			</tbody>
		</table>
	</div>
</div>

</div>
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

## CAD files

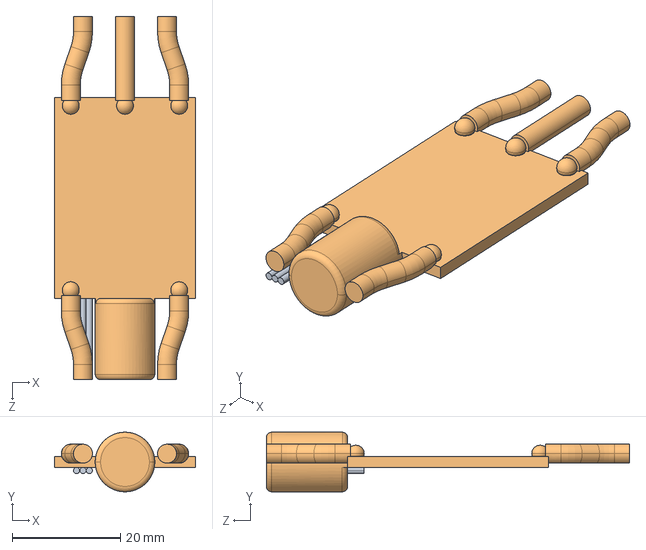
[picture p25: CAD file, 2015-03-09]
besc/cad/BESC30-R1.step
26.0 x 11.0 x 67.0 mm

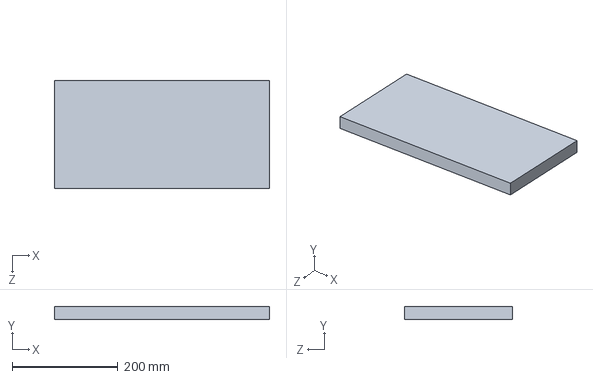
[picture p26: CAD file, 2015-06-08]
float/cad/FLOAT-16X8X1-R1.STEP
406.4 x 25.4 x 203.2 mm

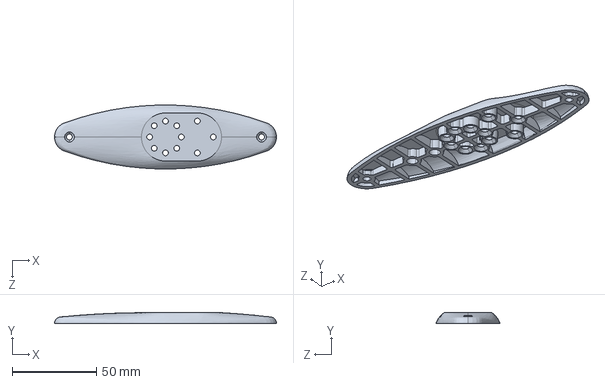
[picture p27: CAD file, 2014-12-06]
thrusters/cad/T100-P-BRACKET-R1.STEP
132.1 x 6.35 x 38.0 mm

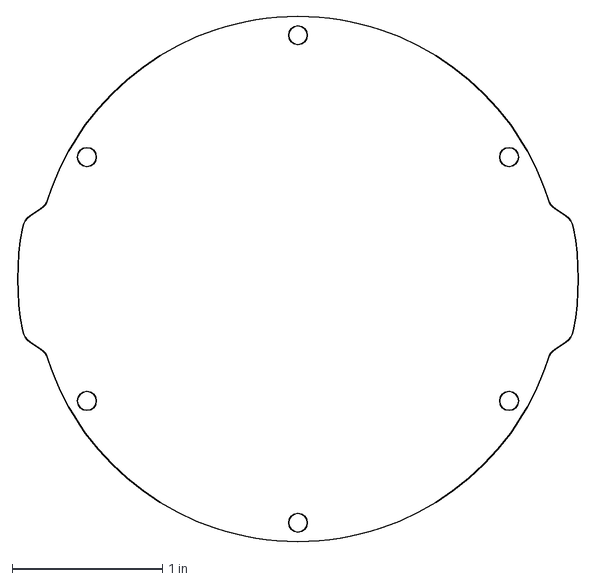
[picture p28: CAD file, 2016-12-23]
wte/dxf/WTE3-P-END-CAP-R1.DXF
3.76 x 3.50 in

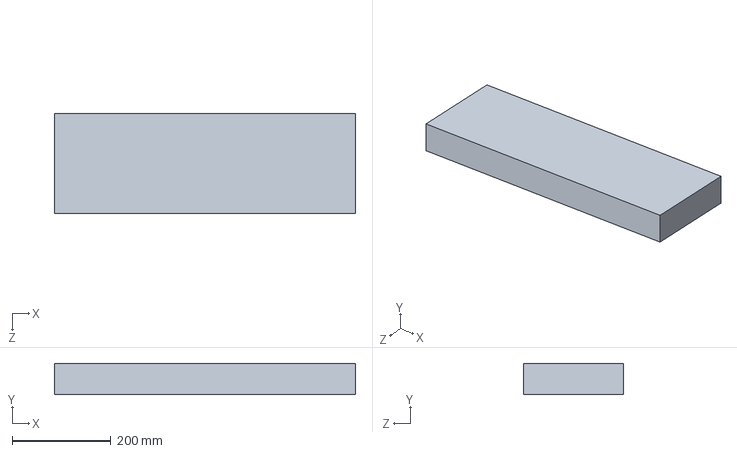
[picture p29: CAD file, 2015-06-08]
float/cad/FLOAT-24X8X2P5-R1.STEP
609.6 x 63.5 x 203.2 mm

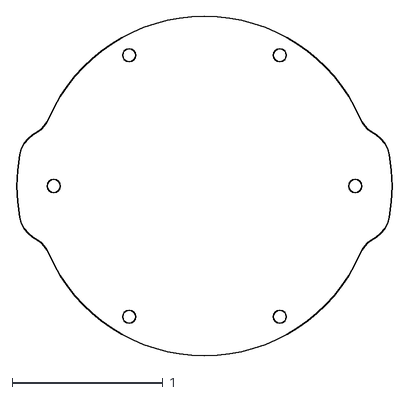
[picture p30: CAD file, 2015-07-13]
wte/dxf/WTE2-P-END-CAP-R1.DXF
2.50 x 2.25

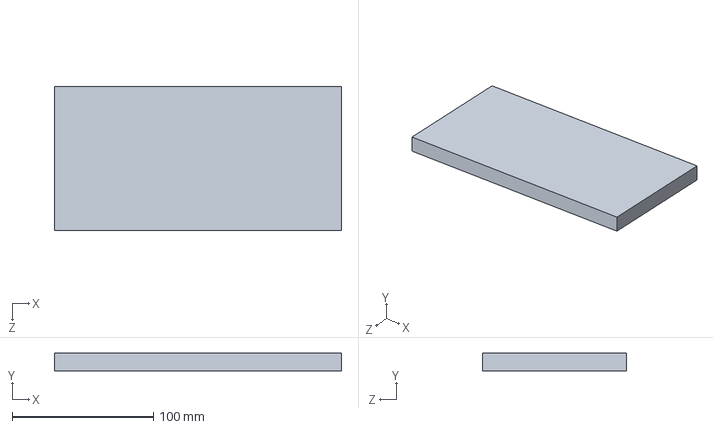
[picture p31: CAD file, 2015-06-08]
float/cad/FLOAT-8X4X0P5-R1.STEP
203.2 x 12.7 x 101.6 mm

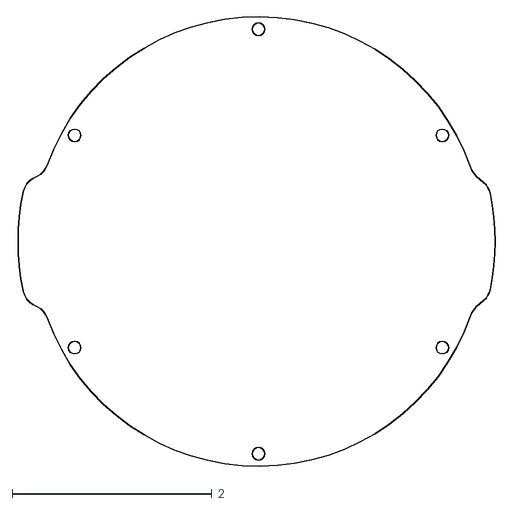
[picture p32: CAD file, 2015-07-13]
wte/dxf/WTE4-P-END-CAP-R1.DXF
4.81 x 4.51

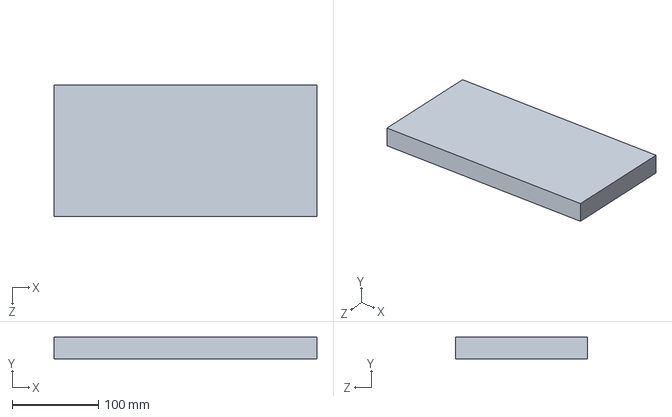
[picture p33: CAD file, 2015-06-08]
float/cad/FLOAT-12X6X1-R1.STEP
304.8 x 25.4 x 152.4 mm

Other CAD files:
besc/cad/BESC30-R1.igs
besc/cad/BESC30-R1.sldprt
besc/cad/BESC30-R1.stl
float/cad/FLOAT-12X6X1-R1.IGS
float/cad/FLOAT-12X6X1-R1.SLDPRT
float/cad/FLOAT-12X6X1-R1.STL
float/cad/FLOAT-16X8X1-R1.IGS
float/cad/FLOAT-16X8X1-R1.SLDPRT
float/cad/FLOAT-16X8X1-R1.STL
float/cad/FLOAT-24X8X2P5-R1.IGS
float/cad/FLOAT-24X8X2P5-R1.SLDPRT
float/cad/FLOAT-24X8X2P5-R1.STL
float/cad/FLOAT-8X4X0P5-R1.IGS
float/cad/FLOAT-8X4X0P5-R1.SLDPRT
float/cad/FLOAT-8X4X0P5-R1.STL
thrusters/cad/T100-P-BRACKET-R1.SLDPRT
thrusters/cad/T100-P-BRACKET-R1.STL

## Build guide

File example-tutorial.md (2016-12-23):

---
layout: tutorial
title: OpenROV Kit Tutorial
order: 0
permalink: /example-tutorial/
nav:
- Introduction: introduction
- - Tools and Supplies: tools-and-supplies
- Step 1 - Remove Motors: step-1-remove-stock-openrov-motors
- Step 2 - Cut Wires: step-2-cut-and-strip-motor-wires

store-links:
- T100 Thruster: http://bluerobotics.com/store/thrusters/t100-thruster/
- M100 Motor: http://bluerobotics.com/store/thrusters/m100-motor/

manual-links:
- T100 Thruster: /thrusters/
- M100 Motor: /thrusters/motors/

tutorial-links:
- Getting Started with the T100 Thruster: /
---

[diagram]: /assets/images/t100-wiring-1.png

# Introduction

This page shows examples of the markdown text that can be used in this documentation.

## Tools and Supplies

* 1.5mm hex key
* Wire cutters
* Wire strippers

# Step 1: Remove Stock OpenROV Motors

The first thing you'll have to do is to remove the stock OpenROV motors to make room for the thrusters.

First, remove the two forward thrusters by removing the set screws followed by the four nuts and bolts.

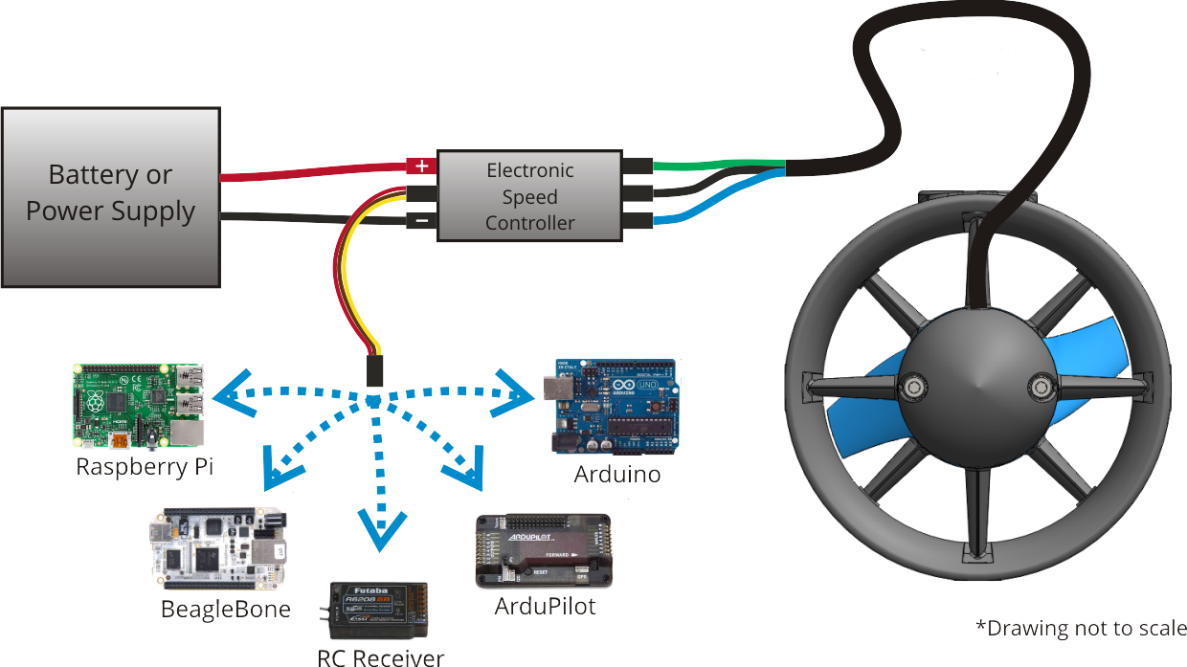
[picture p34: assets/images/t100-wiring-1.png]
diagram


When you're done, it will look like this:

diagram

---

# Step 2: Cut and Strip Motor Wires

Next, you need to cut and strip the old wires from the motors before attaching them to the thruster wires.

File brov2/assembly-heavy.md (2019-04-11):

---
layout: default
title: BlueROV2 Assembly with Heavy Add-On Kit
permalink: /brov2/assembly-heavy/
order: 1
topnavbar: brov2
nav:
- Introduction: assembly-intro
- - Safety: safety
- Required Tools: required-tools-not-included
- What's Included: whats-included
- - Frame: frame
- - Electronics Enclosure: electronics-enclosure
- - Battery Enclosure: battery-enclosure
- - Thrusters: thrusters
- - Fairings: fairings
- - Tether: tether
- - Tools: tools
- - Lights: lights
- - Leak Sensor: sos-leak-sensor
- - Desiccant: desiccant
- - Heavy Variant Add-On Kit: heavy-variant-add-on-kit
- What's Not Included: what-you-need-for-operation-that-is-not-included
- Frame Assembly: assembling-the-frame
- - Battery Enclosure: mounting-the-battery-enclosure-to-the-bottom-panel
- - Center Panels: assembling-the-center-panels
- - Frame: assembling-the-frame-1
- Electronics Overview: electronics-enclosure-overview
- Cable Installation: installing-the-cables
- - Removing Endcap: removing-the-electronics-enclosure-endcap
- - Penetrator Installation: installing-the-penetrators
- - End Cap Installation: installing-the-end-cap
- - Finishing Battery Enclosure: finishing-the-battery-enclosure
- - Optional Preliminary Vacuum Test: optional-preliminary-vacuum-test
- - Penetrator Power Wiring: installing-the-power-wires-from-the-penetrators
- - Penetrator Signal Wiring: installing-the-signal-wires-from-the-penetrators
- - Cable Routing: cable-routing
- Final Assembly: final-assembly
- - Desiccant: adding-desiccant-to-the-electronics-enclosure
- - Mounting Electronics Enclosure: mounting-the-electronics-enclosure-onto-the-frame
- - Mounting Thrusters: mounting-the-thrusters-to-the-frame
- - Install New Thruster Guards: install-new-thruster-guards
- - Mounting Lights: mounting-the-lights
- - Mounting the Tether: mounting-the-tether-to-the-frame
- - External Cable Management: thruster-and-lumen-cable-management
- - Installing Fairings: installing-the-fairings-and-buoyancy
- - Ballast: mounting-ballast-to-the-frame
- Topside Setup: topside-setup
- Next Steps: next-steps

store-links:
- BlueROV2: http://bluerobotics.com/store/rov/bluerov2/
- Heavy Add-On Kit: https://www.bluerobotics.com/store/rov/brov2-heavy-kit/

manual-links:
- Archived Assembly: /brov2/assembly/
- Software Setup: /brov2/software-setup/
- Specifications: /brov2/
- Operations Manual: /brov2/operation/

-redirect: https://www.bluerobotics.com/learn/bluerov2-heavy-configuration-retrofit-kit-installation/

---

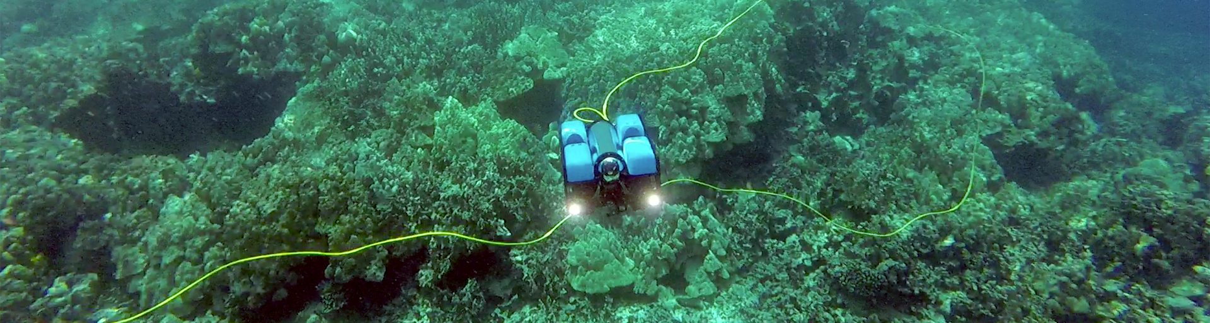
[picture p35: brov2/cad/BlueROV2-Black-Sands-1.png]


# Assembly Intro

The BlueROV2 kit comes almost ready to dive. This document includes instruction for integrating the Heavy Add-On Kit to your initial build. The assembly can be completed with basic hand tools; no soldering or potting is required. We have included a couple of the tools to make assembly and regular use as easy as possible.

## Safety 

<i class="fa fa-exclamation-triangle fa-fw fa-2x text-warning"></i> When working with electricity, especially in water, always practice caution. Always ensure that connections are secure and watertight. Keep your body away from spinning motors and propellers.

<i class="fa fa-exclamation-triangle fa-fw fa-2x text-warning"></i> When working with silicone grease and threadlocker, take care to minimize skin contact. Wear protective nitrile or PVC gloves when handling.

# Required Tools (Not Included)

- \#2 Phillips head screwdriver 
- Wire cutters or scissors (for cutting zip ties)
- Medium-strength (blue) threadlocker such as [Loctite 243](https://www.amazon.com/Loctite-1330799-Resistant-thread-locker-6-milliliter/dp/B004L439FE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)
- Isopropyl alcohol or isopropyl alcohol wipes
- Vacuum pump such as [this one](https://www.amazon.com/HFS-Brake-Bleeder-Vacuum-Tuner/dp/B00NP60URE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)
- 2 mm flat head screw driver

# What's Included

## Frame

Quantity      | Part														| Usage
------------- | ------------------------------------------------------------| ----------------------
2             | Front center panel (1/2" thick black HDPE)        			|    
2             | Rear center panel (1/2" thick black HDPE)           		|     	       
1             | Bottom panel (1/2" thick black HDPE)                       	|  
2             | Side panel (3/8" thick black HDPE)                       	|
2             | Enclosure Cradle (4" Series) (black anodized aluminum)  	| Mounting the electronics enclosure to the frame
8 			  | M4x18 socket head cap screw (316 stainless steel)           | Mounting the electronics enclosure cradles to the frame        
12            | M5x16 button head cap screw (316 stainless steel)           | Assembling the frame
7             | 8-16 thread, 5/8" long, thread-forming screw                | Mounting the ballast to the frame                         
7             | Ballast Weight (200g, 7 oz)									| 

## Electronics Enclosure                                                         

Quantity      | Part																		| Usage
------------- | ----------------------------------------------------------------------------| ---------------
1             | Electronics Tray (4" Series)                                                |                      
1             | Watertight Enclosure for ROV/AUV w/ Dome End Cap installed                | Electronics enclosure          
1             | Aluminum End Cap with 14 Holes w/ 3 Cable Penetrator Blank, 1 Bar30 Pressure Sensor, 1 Enclosure Vent and Plug, and 1 power cable (installed)	|
1             | Set of tether board power wires (installed)								| Provided power to the tether board
4             | M3x16 socket head cap screw (316 stainless steel)  							| Mounting the electronics enclosure to the electronics enclosure cradle
1			  | Fathom-X Tether Interface Board installed									| Long distance ethernet connection
1			  | 3DR Pixhawk (installed)														| Autopilot
1             | I<sup>2</sup>C Splitter with cable											| Allows for up to 4 I<sup>2</sup>C devices
1			  | Raspberry Pi 3 (installed)													| Companion computer
1			  | Raspberry Pi Camera 2 (installed)   										| Camera
1			  | Pixhawk Power Module (installed) 											| Powers the Pixhawk and monitors current and battery voltage
2             | Universal Battery Elimination Circuit (UBEC) (installed)                    | Powers the Raspberry Pi and Pixhawk servo rails         

## Battery Enclosure

Quantity      | Part																		| Usage
------------- | ----------------------------------------------------------------------------| ------------------------
2             | Enclosure Clamp (3" Series) (black anodized aluminum w/ rubber strip)   	| Mounting the battery enclosure to the frame       
1             | Watertight Enclosure for ROV/AUV (3" Series)                       			| Battery Enclosure
1             | Aluminum End Cap (3" Series)    				  							|
1             | Aluminum End Cap with 4 Holes (3" Series) w/ 2 blank penetrators and 1 vent installed (anodized aluminum 6061)  |                                                              
1             | XT90 to 3.5 mm bullet connector adapter										| Adapting power wire connector to battery connector
4             | M4x14 socket head cap screw (316 stainless steel)   						| Mounting the battery cradle to the frame
4             | M3x12 socket head cap screws (316 stainless steel)             				| Connecting the battery cradles to each other    
1			  | 1 1/2" long x 3/8" diameter heat shrink										| Battery cable strain relief       

## Thrusters

Quantity      | Part													| Usage
------------- | --------------------------------------------------------|--------------
3   		  | T200 Thrusters w/ Clockwise Propeller installed			|
3 			  | T200 Thrusters w/ Counter-Clockwise Propeller installed |      
16            | M3x16 socket head cap screw (316 stainless steel)      	| Mounting thrusters 1, 2, 3, and 4 to the frame
8 			  | M3x12 socket head cap screw (316 stainless steel)		| Mounting thrusters 5 and 6 to the frame
30            | 5 1/2" zip ties (nylon)									| Routing the thruster and lumen cables

## Fairings

Quantity      | Part															
------------- | ------------------------------------------------------------------------| ---------------------
4             | BlueROV2 Fairings (blue polycarbonate)               					|
4             | Subsea Buoyancy Foam (R-3318 urethane foam)                        		|
16            | #4 size, 3/4" long pan head self tapping screw (316 stainless steel)    | Mounting the fairings and buoyancy to the frame                               

## Tether

Quantity      | Part														| Usage 
------------- | ------------------------------------------------------------|--------------
1             | Fathom Tether w/ installed Cable Penetrator for 8 mm Cable (25-300m)           	|
1             | Tether Cable Thimble                       					| Mounting the tether to the frame	
5             | Heavy Duty Zip Ties											| Mounting the tether to the thimble and frame            

## Tools                                                      

Quantity      | Part													| Usage
------------- | --------------------------------------------------------| ---------------
1             | Silicone Grease - 10g Tube								| Lubricate O-rings prior to installation 
1             | O-Ring Pick   											| Remove and install O-rings
1             | 2.5 mm hex driver										| Install M3 screws 
1			  | #1 Phillips head screwdriver    						| Install the fairing screws 
1			  | Penetrator Wrench             					        | Install penetrators
1			  | 1.5 mm hex key											| Thruster dissassembly
1			  | 2 mm hex key											| Change propellers
1			  | 3 mm hex key									     	| Install M4 and M5 screws
1			  | MicroSD to SD Adapter 									| 

## Lights

Quantity      | Part
------------- | --------------------------------------------------------
1-2           | Lumen Subsea Light w/ Mounts (Pair, Pre-Connected) (Optional)     

## SOS Leak Sensor

Quantity      | Part
------------- | ------------------------------------------------------------
1             | SOS Leak Sensor Probe Host Board (installed)
2             | 6" Probe (installed)
2             | 12" Probe (installed)
20            | Replacement SOS Probe Tips
1 			  | Test Cable

## Desiccant 

(Added to all ROVs ordered after February 14, 2018)

Quantity      | Part
------------- | ------------------------------------------------------------
1             | 150 gram container of Moisture Indicating Silica Gel Desiccant
3			  | Desiccant Bags

## Spares (Added to all ROVs ordered after February 14, 2018)

Quantity      | Part                      | Usage
------------- | ------------------------- | -----------------
1             | Cable Penetrator Blank    | Fill the hole for Lumen Penetrator if you aren't using Lumens
2			  | 013 O-ring                | Extra penetrator O-rings
1             | Cable Penetrator Nut      | Used with Cable Penetrator Blank if you aren't using Lumens

## Heavy Variant Add-On Kit

Quantity      | Part                      | Usage
------------- | ------------------------- | -----------------
2             | Heavy Fairing   		  | Retains Heavy Buoyancy Blocks
2             | Heavy Guard   		  | Protects outer Thrusters from damage
8	      | Heavy Guard Mounting Bracket                | Allows Heavy Guard to be attached to ROV frame
2             | Heavy Additional Buoyancy Block      | Increases buoyancy to offset additional ROV weight
2             | Basic ESC-R3   		  | Additional ESCs to drive the extra Thrusters
1             | T200 Thruster w/ Clockwise Propeller installed   		  | 
1             | T200 Thrusters w/ Counter-Clockwise Propeller installed            |
8	      | M3x12 socket head cap screw (316 stainless steel)      | Installing Thrusters 7 and 8 to Frame
2             | 3 Pole Euro Terminal Block        | Connecting thruster power wires to ESC power wires
12            | M4x12 socket head cap screw (316 stainless steel)      | Attaching Guard Mounting Brackets to Frame
4             | #4 x 3/8" Thread Forming Screw for Plastic             | Attaching Guard Mounting Brackets 
4             | Fairing Screws (T200 Nozzle Screws)          | Attaching new Heavy Fairings to Original Fairings
30            | 5.5" Zip Ties       | Cable Management
3             | Ballast Weight (200g, 7 oz)      | 
3             | 8-16 thread, 5/8" long, thread-forming screw                | Mounting the ballast to the frame 

## What You Need for Operation that is Not Included 

There are some items necessary for operation that are not included with the kit. 

 - A gamepad controller. We recommend [an Xbox360 Controller](https://www.amazon.com/Microsoft-Wired-Controller-Windows-Console/dp/B004QRKWLA?th=1) or [a Logitech F310 Gamepad](http://gaming.logitech.com/en-us/product/f310-gamepad).
 - A laptop or a Windows tablet. QGroundControl works on Mac, Windows, and Linux.
 - A battery for the BlueROV2. We recommend getting our [18AH Lithium-ion Battery](http://www.bluerobotics.com/store/electronics/batteries/battery-li-4s-18ah-r1/) or 2 or 3 of [these](http://www.hobbyking.com/hobbyking/store/uh_viewItem.asp?idProduct=56844)
 - A 4S capable LiPo/Li-Ion balance battery charger. We use and recommend [this one](https://hobbyking.com/en_us/turnigy-reaktor-300w-20a-ac-dc-synchronous-balance-charger-discharger-us-plug.html).
 
# Assembling the Frame

## Mounting the Battery Enclosure to the Bottom Panel

To mount the battery enclosure to the bottom panel you will need the following parts and tools:

- 2 x Enclosure Clamp (3" Series)
- 1 x Threadlocker 
- 1 x Bottom panel 
- 1 x Bag with four M4x14 socket head cap screws and four M3x12 socket head cap screws
- 1 x Watertight Enclosure for ROV/AUV (3" Series)
- 1 x 3 mm hex key
- 1 x 2.5 mm hex driver

1. Remove the Aluminum End Cap with 4 Holes (3" Series) to open the Watertight Enclosure for ROV/AUV (3" Series) and set the bags inside of it to the side, except for the bag with four M4x14 and four M3x12 screws in it.

2. Apply one drop of threadlocker to the bottom of each M4x14 socket head cap screw. Roll the screws around on a paper towel to evenly spread the threadlocker and to remove excess threadlocker.

	

3. Attach one of the Enclosure Clamps (3" Series) to the bottom panel using the four M4x14 socket head cap screws. Be sure that the screw head is in the [counterbore](https://en.wikipedia.org/wiki/Counterbore). The bottom panel is only counterbored on one side. Tighten the screws until you can feel them start to dig into the bottom panel.

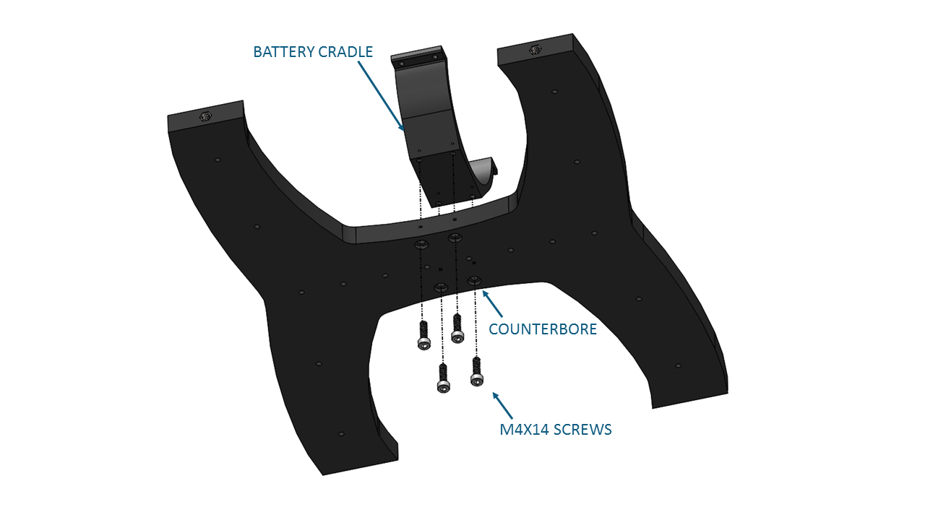
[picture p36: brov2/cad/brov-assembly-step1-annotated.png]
	 

4. Apply one drop of threadlocker to each of the 4 M3x12 screws. Roll the screws around on a paper towel to evenly spread the threadlocker and to remove excess threadlocker.

6. Place the Watertight Enclosure for ROV/AUV (3" Series) between the two Enclosure Clamps (3" Series) and install the four M3x12 screws into the Enclosure Clamps (3" Series). Note that each of the Enclosure Clamps (3" Series) are tapped on only one side. Install all four screws loosely at first and then slowly tighten them on both sides evenly. Take care not to overtighten the screws. Keep the battery enclosure approximately centered in the Enclosure Clamps (3" Series).

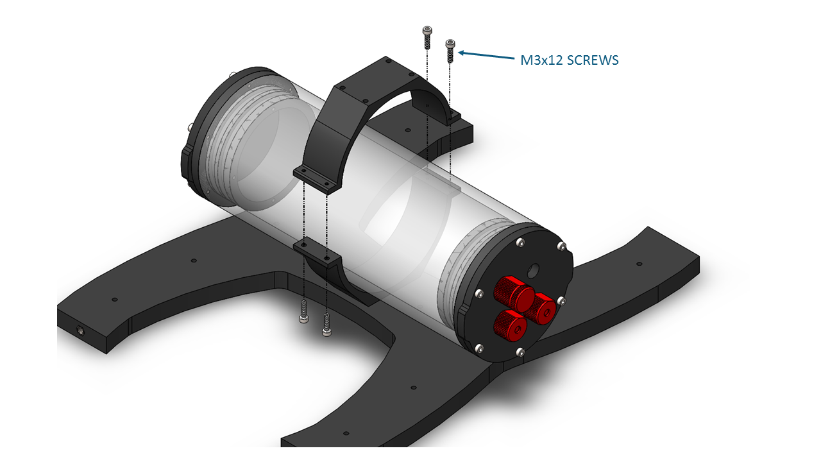
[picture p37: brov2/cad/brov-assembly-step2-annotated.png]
	

	When you are finished tightening the screws, both sides should look similar to this.

	
	
## Assembling the Center Panels

To assemble the center panels you will need the following parts and tools:

- 2 x Enclosure Cradle (4" Series)
- 2 x Front center panels 
- 2 x Rear center panels 
- 1 x Threadlocker 
- 1 x Bag with eight M4x18 socket head cap screws 
- 1 x 3 mm hex key 

1. Apply one drop of threadlocker to each of the eight M4x18 screws. Roll the screws around on a paper towel to evenly spread the threadlocker and to remove excess threadlocker.

2. Attach one of the Enclosure Cradle (4" Series) to the rear center panels. Tighten the screws until they indent the rear center panels slightly. 

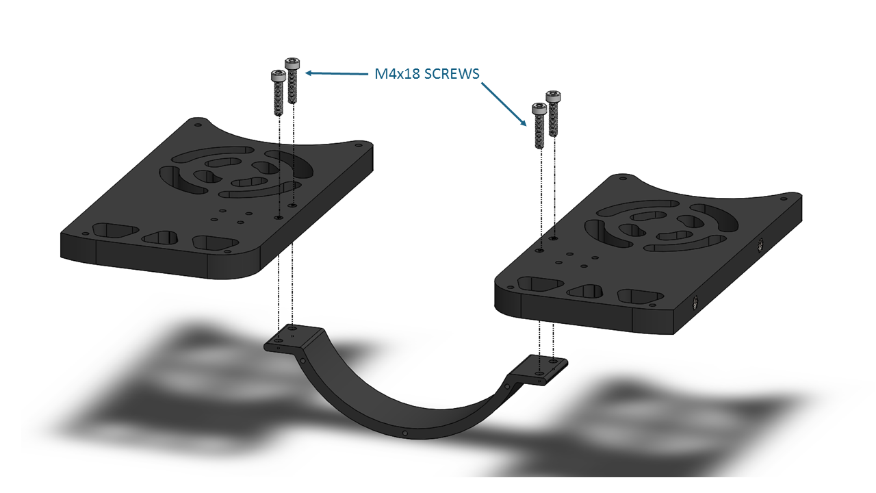
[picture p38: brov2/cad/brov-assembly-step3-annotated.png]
	
	
3. Attach the other Enclosure Cradle (4" Series) to the front center panels. Tighten the screws until they indent the front center panels slightly. 

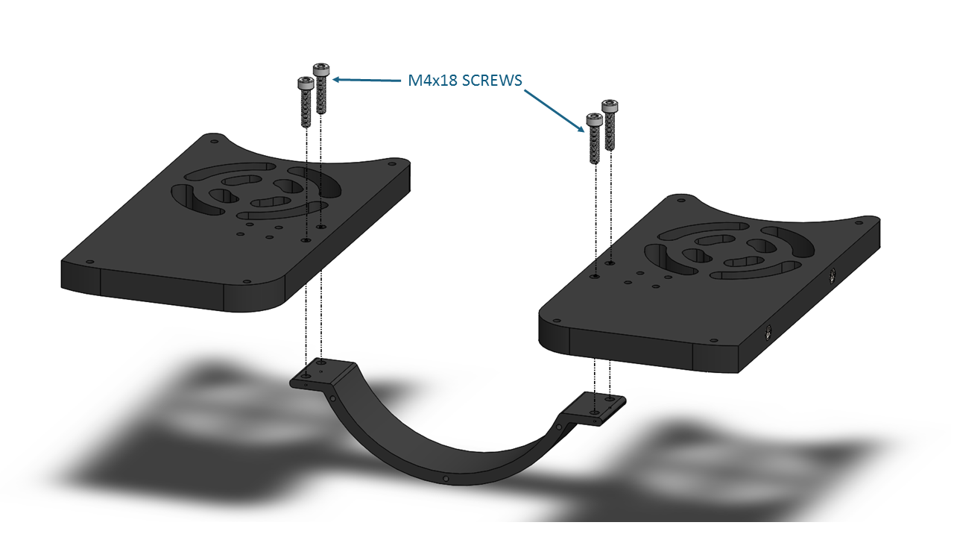
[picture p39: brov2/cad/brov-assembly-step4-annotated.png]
	
	
## Assembling the Frame

To assemble the frame you will need the following parts and tools:

- 1 x Threadlocker 
- 1 x Bag with 12 M5x16 button head cap screws 
- 2 x Side panels
- 1 x Bottom panel with the Watertight Enclosure for ROV/AUV (3" Series) installed
- 1 x Front center panel assembly
- 1 x Rear center panel assembly
- 1 x 3 mm hex key

1. Apply one drop of threadlocker to each of the 12 M5x16 screws. Roll the screws around on a paper towel to evenly spread the threadlocker and to remove excess threadlocker.
	
2. Install both side panels to the bottom panel using four of the M5x16 screws; the Aluminum End Cap (3" Series) on the Watertight Enclosure for ROV/AUV (3" Series) should be on the same side as the Lumen mounting holes. **It is very important to avoid overtightening these screws.** Tighten these screws using the provided 3 mm hex key. Hold the short end of the 3 mm hex key while you are tightening the M5x16 screws. Do not tighten beyond the tightness you can achieve holding the short end of the 3 mm hex key. 

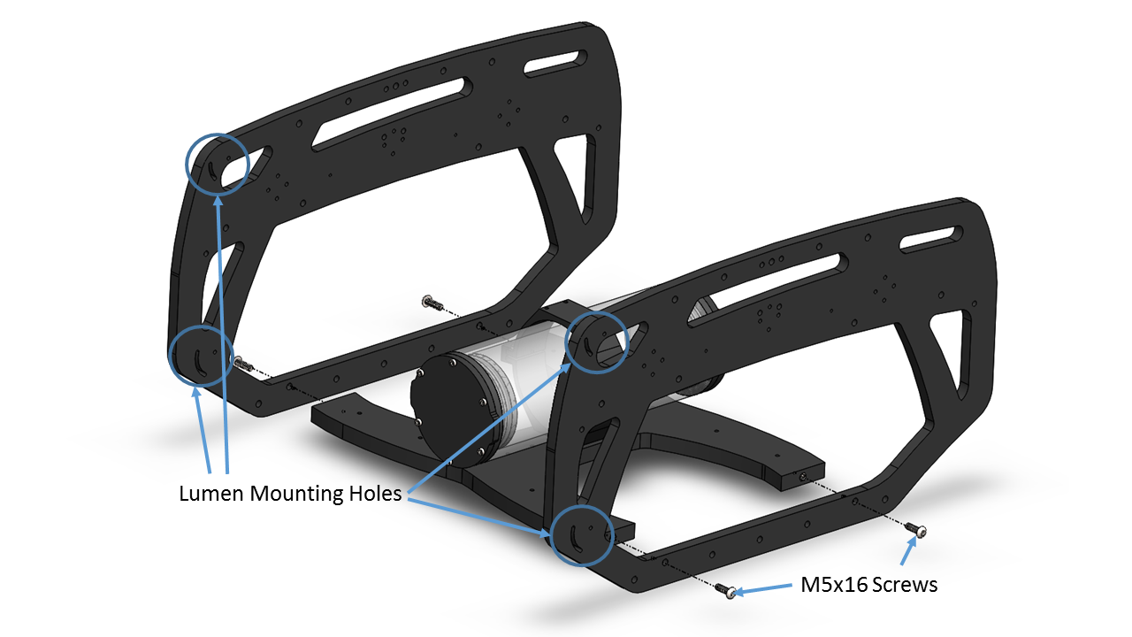
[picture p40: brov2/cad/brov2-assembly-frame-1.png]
	
	
3. Install the center panel assemblies to the side panels using the remaining eight M5x16 screws. **It is very important to avoid overtightening these screws.** Tighten these screws using the provided 3 mm hex key. Hold the short end of the 3 mm hex key while you are tightening the M5x16 screws. Do not tighten beyond the tightness you can achieve holding the short end of the 3 mm hex key.

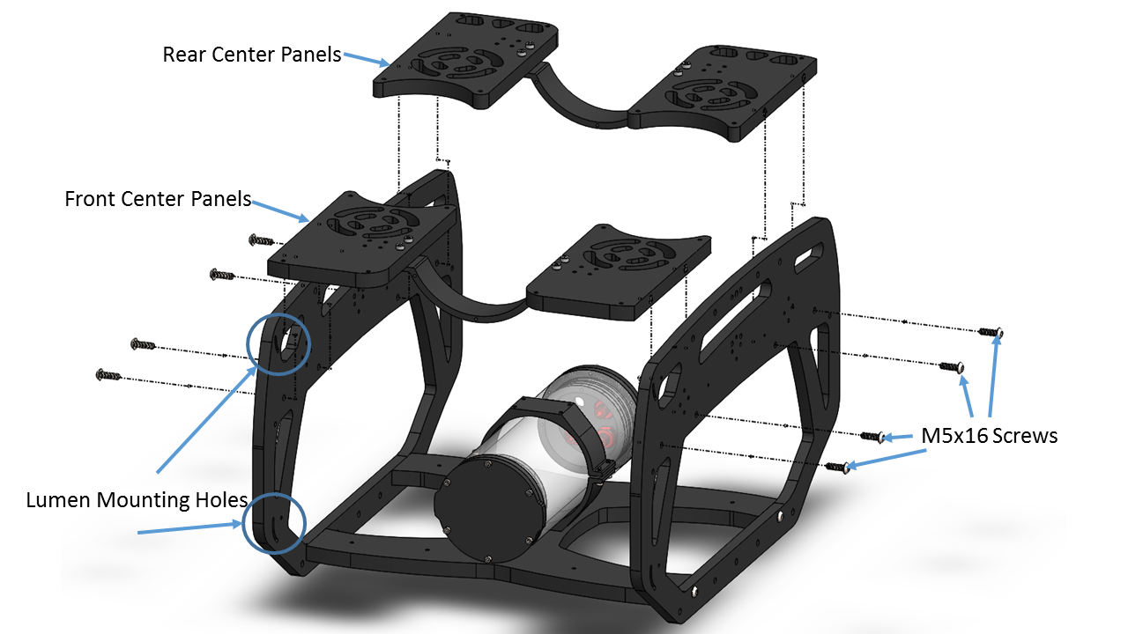
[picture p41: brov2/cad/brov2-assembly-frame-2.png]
	
	
Now the BlueROV2 should look like the picture below. 

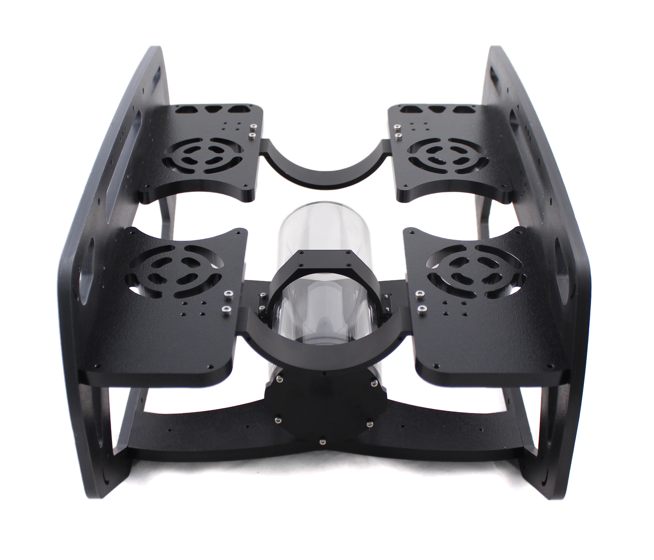
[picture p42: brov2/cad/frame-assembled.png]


# Electronics Enclosure Overview

The images below show orientation of the main pieces of hardware in the electronics enclosure. They also point out the names of several of the important parts for assembly that will be discussed in the remaining instrustions.

<b> <font size="4"> Top View </font> </b> 
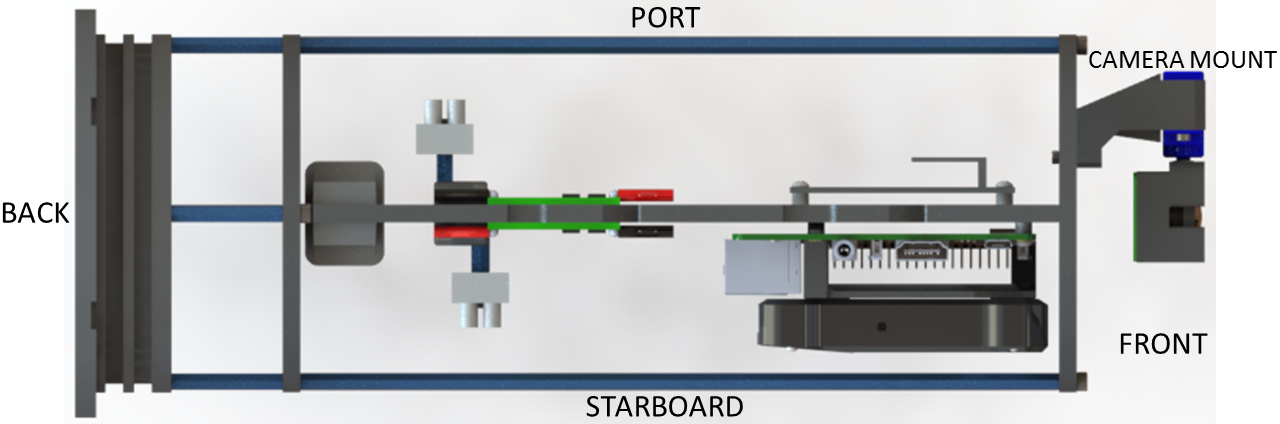
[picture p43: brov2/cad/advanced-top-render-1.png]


<b> <font size="4"> Starboard View </font> </b> 
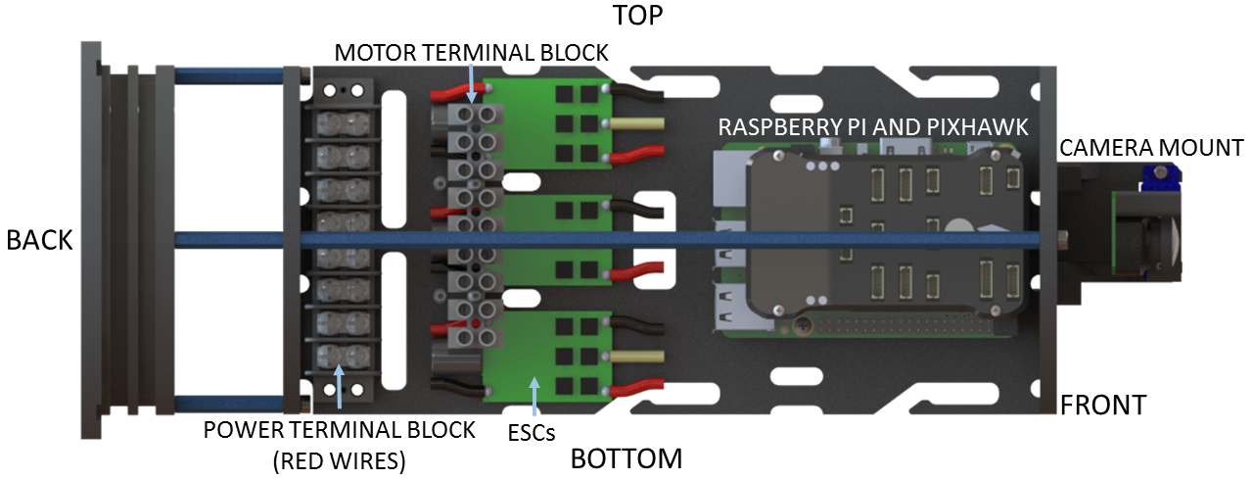
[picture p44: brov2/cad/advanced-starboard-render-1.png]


<b> <font size="4"> Port View </font> </b> 
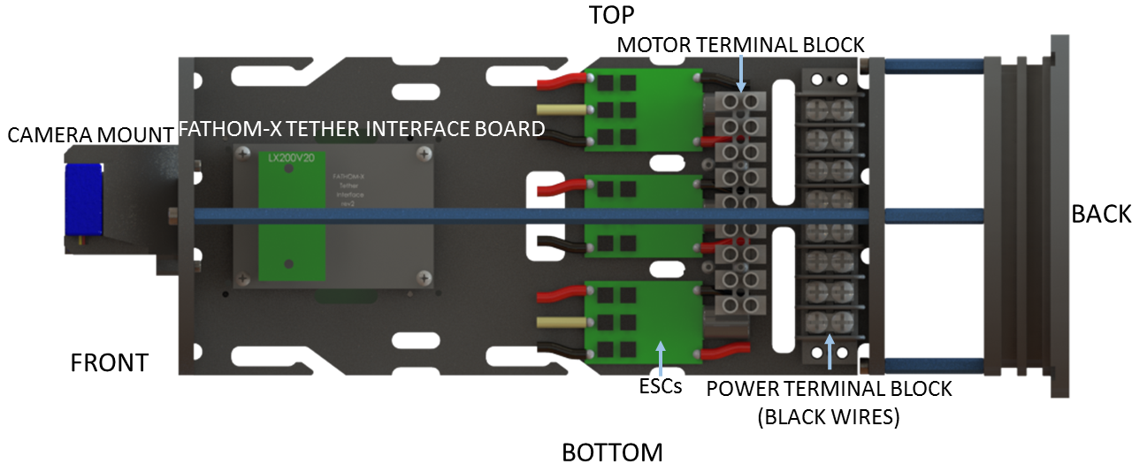
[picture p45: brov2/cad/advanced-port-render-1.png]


<b> <font size="4"> Front View </font> </b> 
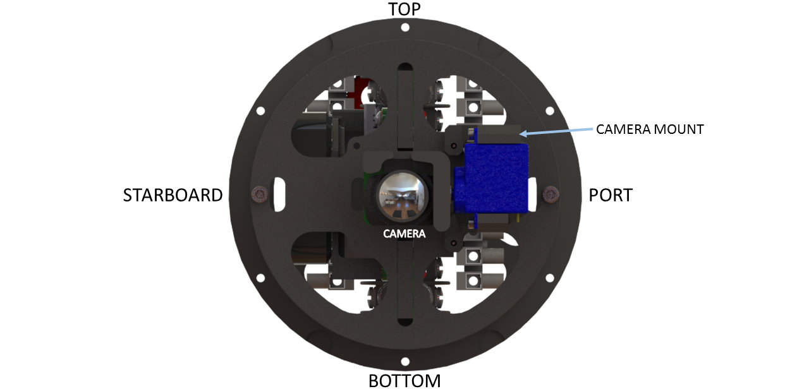
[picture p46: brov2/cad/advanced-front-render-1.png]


# Installing the Cables 

## Removing the Electronics Enclosure Endcap

The endcap will need to be removed from the electronics enclosure in order to install the cable penetrators. To remove the endcap you will need the following parts and tools:

- 1 x Large flat head screw driver (Optional)
- 1 x The electronics enclosure assembly
- 1 x 2.5 mm key driver 

1. Remove the Watertight Enclosure for ROV/AUV with Dome End Cap installed from the rear O-Ring Flange (4" Series). If this step is difficult, you can place a large flat head screwdriver into the slots on the O-Ring Flange (4" Series), and then twist to get a gap between the acrylic tube and the O-Ring Flange (4" Series). Once you have the gap, you can wedge a screw driver between the end of the acrylic tube and the O-Ring Flange (4" Series) to finish removing the acrylic tube.

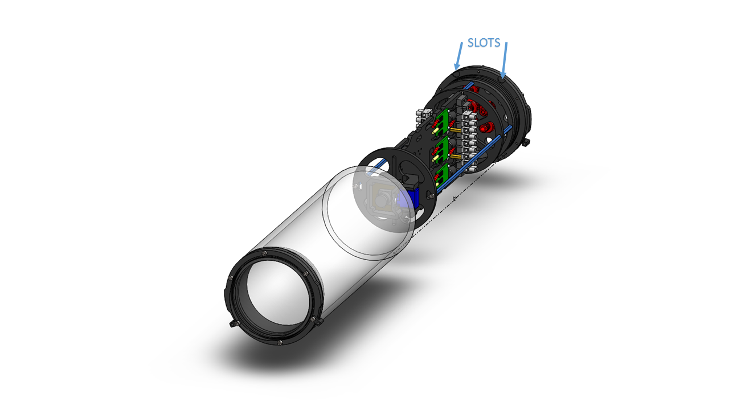
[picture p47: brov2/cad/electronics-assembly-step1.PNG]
	
		
2. Remove the Aluminum End Cap with 14 Holes by removing the six M3x12 screws using the M2.5 hex driver. Place the M3x12 screws, clips (small L-shaped parts), and face seal O-ring in a safe place. 

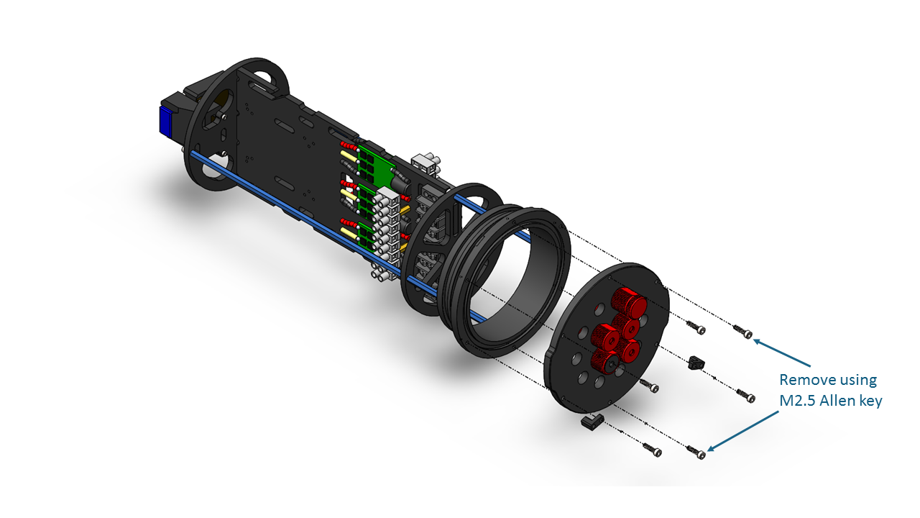
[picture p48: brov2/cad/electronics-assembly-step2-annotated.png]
	
	
3.	Remove the two blank penetrators as pictured from the 4” End Cap with the penetrator wrench that came with the BlueROV2 kit.

## Installing the Penetrators

To install the Penetrators you will need the following parts and tools:

- 1 x Bag with one Cable Penetrator Nut (black), eight Cable Penetrator Nut (red), and nine O-rings
- 1 x Silicone Grease - 10g Tube
- 1 x Aluminum End Cap with 14 Holes w/ 1 Cable Penetrator Blanks, 1 Bar30 Pressure Sensor, 1 Enclosure Vent and Plug, and 1 power cable installed
- 4 x T200 with counter-clockwise thrusters 
- 4 x T200 with clockwise thrusters 
- 1 x Set of Lumen lights (optional)
- 1 x Fathom ROV Tether
- 1 x Penetrator Wrench

The Aluminum End Cap with 14 Holes comes with 1 Cable Penetrator Blanks, 1 Bar30 Pressure Sensor, 1 Enclosure Vent and Plug, and 1 power cable installed. (Image Coming soon)

[//]: # ()

If you install the remaining penetrators as shown in the diagram below, it will keep everything neat and organized. (Image Coming soon)

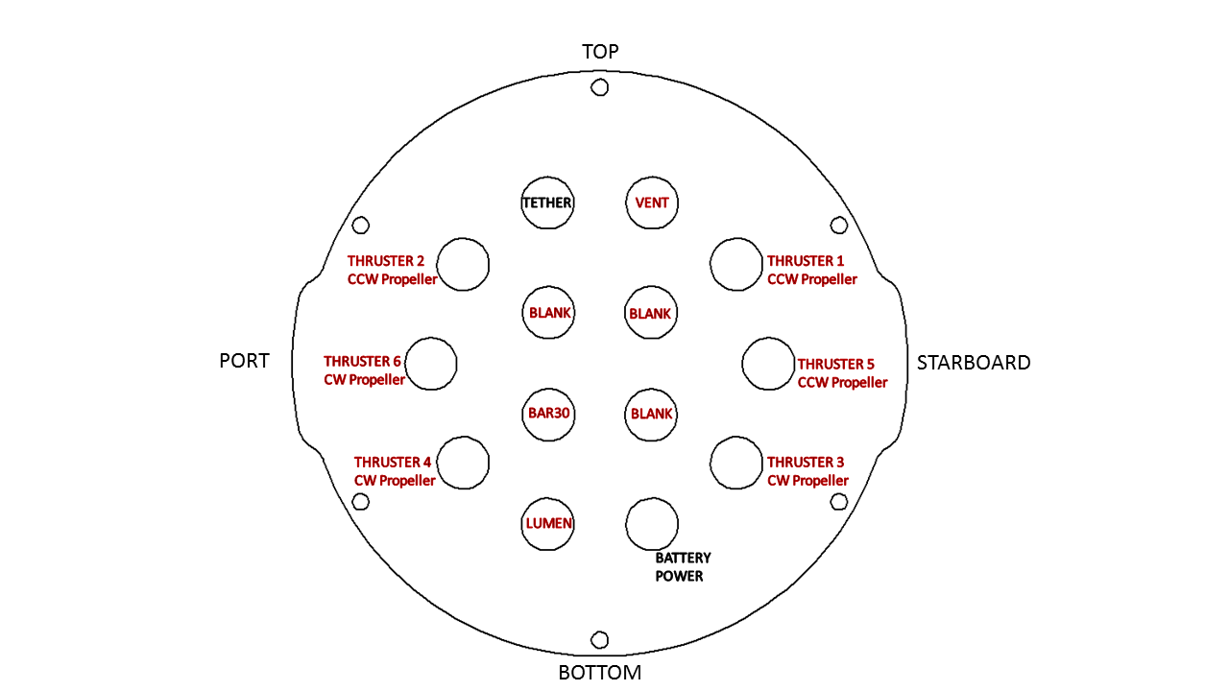
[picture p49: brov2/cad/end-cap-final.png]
[//]: # ()
	
1. Remove ten of the O-rings and apply silicone grease to them. Keep the other O-ring in the bag, you will need it in a minute.

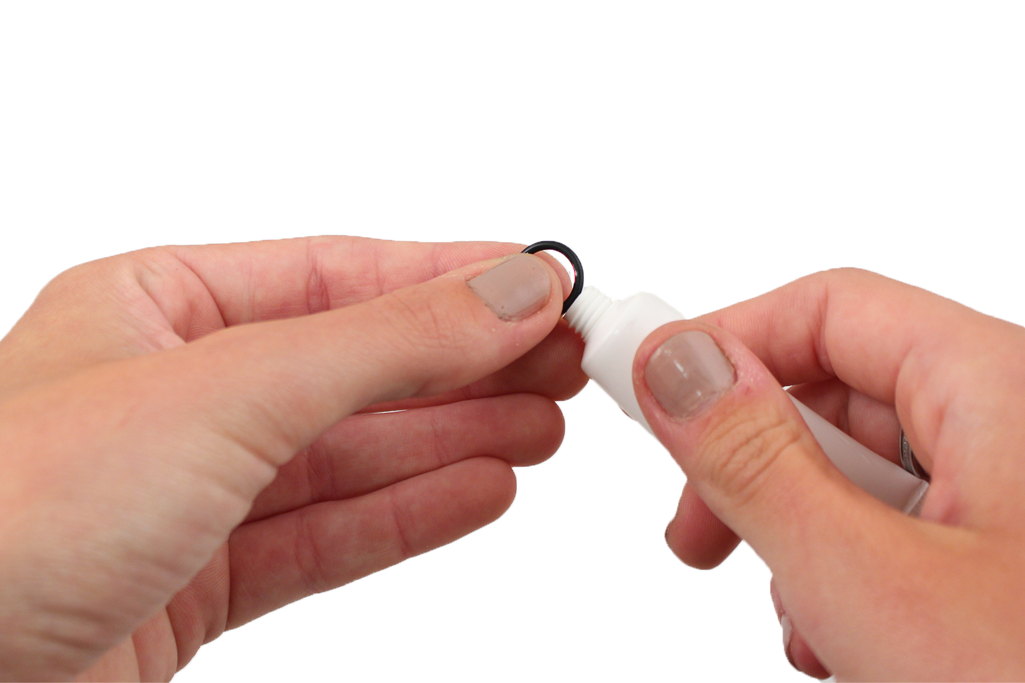
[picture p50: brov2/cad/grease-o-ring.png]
	

2. Wipe the exterior surface of the electronics enclosure endcap clean, and make sure it is free of any particles in the areas where the penetrator O-rings will sit.

3. Install the O-rings onto all of the thruster penetrators, the lumen penetrator, and the tether penetrator. 

4. Install the penetrators to the end cap in the order shown below. Tighten to finger tight, then use the provided wrench to tighten them an additional ~1/16 of a turn. If you can't loosen them with your fingers, they are tight enough. 

	1. Thruster 7 (CW propeller) with red penetrator nut.
	2. Thruster 8 (CCW propeller) with red penetrator nut.
	3. Thruster 1 (CCW propeller) with red penetrator nut
	4. Thruster 5 (CCW propeller) with red penetrator nut
	5. Thruster 3 (CW propeller) with red penetrator nut
 	6. Lumen with red penetrator nut
	7. Thruster 4 (CW propeller) with red penetrator nut
	8. Thruster 6 (CW propeller) with red penetrator nut
	9. Thruster 2 (CCW propeller) with red penetrator nut
	10. Tether with black penetrator nut

## Installing the End Cap

To reinstall the Aluminum End Cap with 14 Holes you will need the following parts and tools:

- The face seal O-ring, the 6 M3x12 screws, and the clips that you removed from the end cap earlier
- 1 x Silicone Grease - 10g Tube
- 1 x Aluminum End Cap with 14 Holes with all Cable Penetrators and Blank Penetrators installed
- 1 x 2.5 mm hex driver

1. Clean the O-ring and make sure that it is free of any debris or damage. 

2. Clean the O-Ring Flange (4" Series) and make sure that the O-ring groove is free of any debris or damage.

3. Apply Silicone grease to the O-ring.

4. Install face seal O-ring onto the O-Ring Flange (4" Series). 

5. Apply one drop of threadlocker to each of the M3x12 screws. Roll the screws around on a paper towel to evenly spread the threadlocker and to remove excess threadlocker.
	
6. Install Aluminum End Cap with 14 Holes with all Cable Penetrators and Blank Penetrators installed onto the O-Ring Flange (4" Series). Do not fully tighten any screws when first installing them; it may cause the O-ring to slip out of its groove. The end cap's orientation when installed should match the image below. Make sure that the clips are oriented correctly. One should be just right of the Thruster 3 penetrator, and the other should be just left of the Thruster 4 penetrator. 

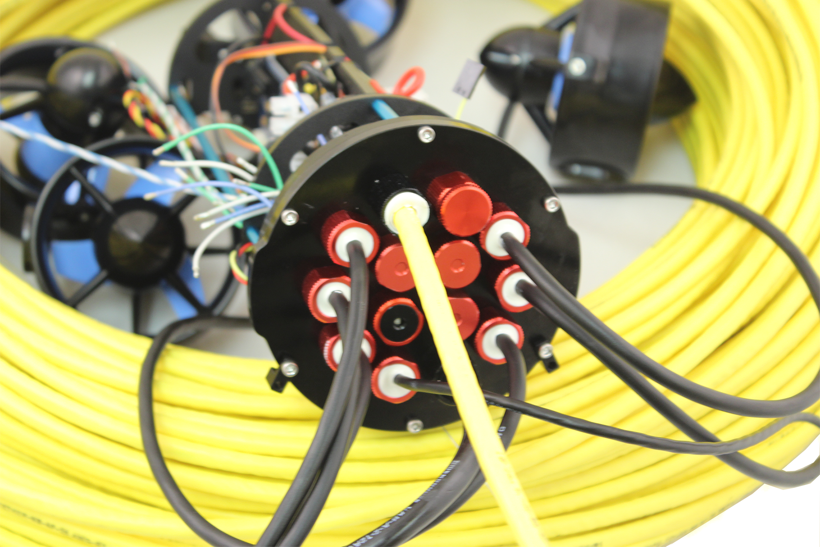
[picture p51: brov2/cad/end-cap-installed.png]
	

## Finishing the Battery Enclosure

To complete the assembly of the battery enclosure you need the following parts and tools:

- 1 x Bag with one red penetrator nut and one O-ring left in it
- 1 x Silicone Grease - 10g Tube
- 1 x End Cap with 4 Holes (3" Series)
- 1 x Penetrator wrench
- 1 x XT90 to 3.5 mm bullet connector adapter
- 1 x 1.5 inch piece of heat shrink
- 1 x Heat gun, hairdryer, or lighter

1. Apply silicone grease to the O-ring.

2. Install the O-ring onto the battery power cable penetrator.
	
3. Install the battery power cable penetrator into the opening in the battery end cap.

4. Place the 1.5 inch long piece of black heat shrink over the end of the battery power cable penetrator. 

5. Apply heat to the heat shrink using your heat gun, hairdryer, or lighter until the heat shrink is firmly attached to the penetrator and snug to the two wires. You should be able to see the threads in the penetrator through the heat shrink.

	

6. Install the XT90 to bullet connector adapter to the battery power wire. 

	

7. If you wish to do the Optional Preliminary Vacuum Test, remove the Vent Plug from the Vent Penetrator Bolt and install the endcap onto the battery enclosure. You will also need to remove the Vent Plug for the Vent Penetrator Bolt on the electronics enclosure.

## Optional Preliminary Vacuum Test

This is the best point in the assembly process to perform a vacuum test. Since you have installed all of the penetrators, but have not done any of the wiring, troubleshooting will be as easy as possible. To prepare for the vacuum test you need to purchase a vacuum pump. We recommend [this one](https://www.amazon.com/HFS-Brake-Bleeder-Vacuum-Tuner/dp/B00NP60URE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).

1. Install the Watertight Enclosure (4" Series) with installed Dome onto the O-Ring Flange (4" Series) that is attached to the Aluminum End Cap with 14 Holes (4" Series)

	

2. Assemble the vacuum tee.

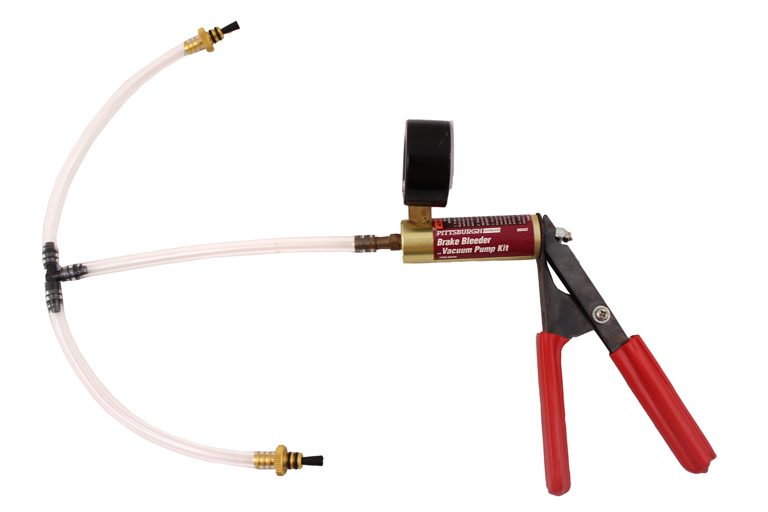
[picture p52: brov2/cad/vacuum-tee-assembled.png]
	

Now you are ready to perform the preliminary vacuum test.

1. Test your vacuum pump to ensure that it is not leaking. See our [Testing the Test Setup Tutorial](http://docs.bluerobotics.com/tutorials/vacuum-test-plug/#testing-the-test-setup) for detailed instructions. 

2. Insert one of the vacuum plugs into the battery enclosure vent penetrator.

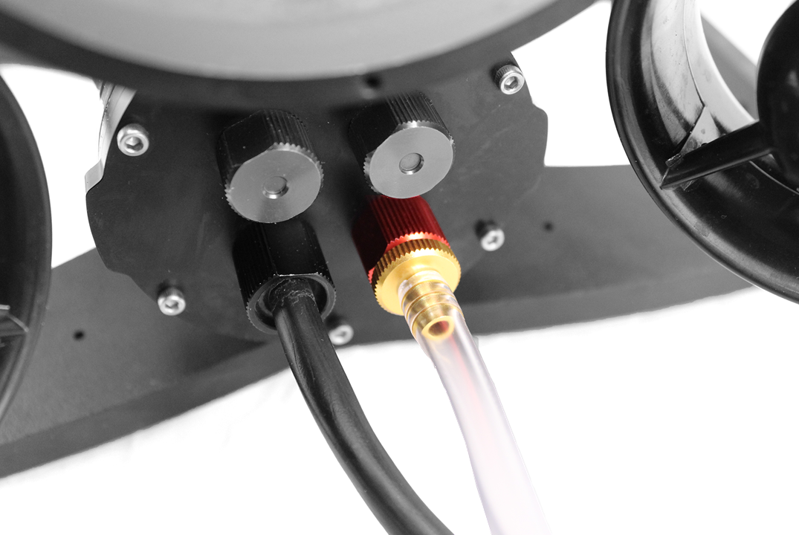
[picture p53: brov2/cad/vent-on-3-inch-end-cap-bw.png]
	

3. Insert the other vacuum plug into the electronics enclosure vent penetrator.

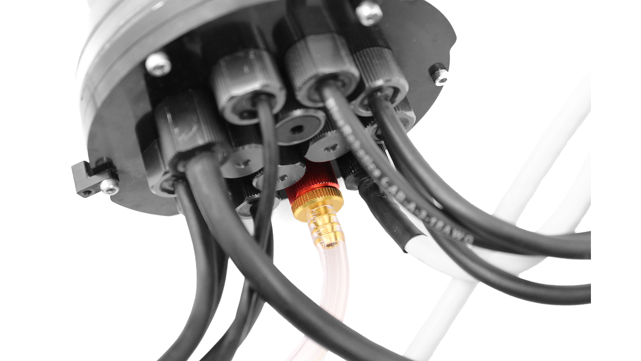
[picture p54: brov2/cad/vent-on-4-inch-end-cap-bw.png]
	

4. Pump the vacuum until the gauge reads 10 in. Hg [34 kPa] vacuum. If you cannot pull a vacuum, try the suggestions following step 6, below.

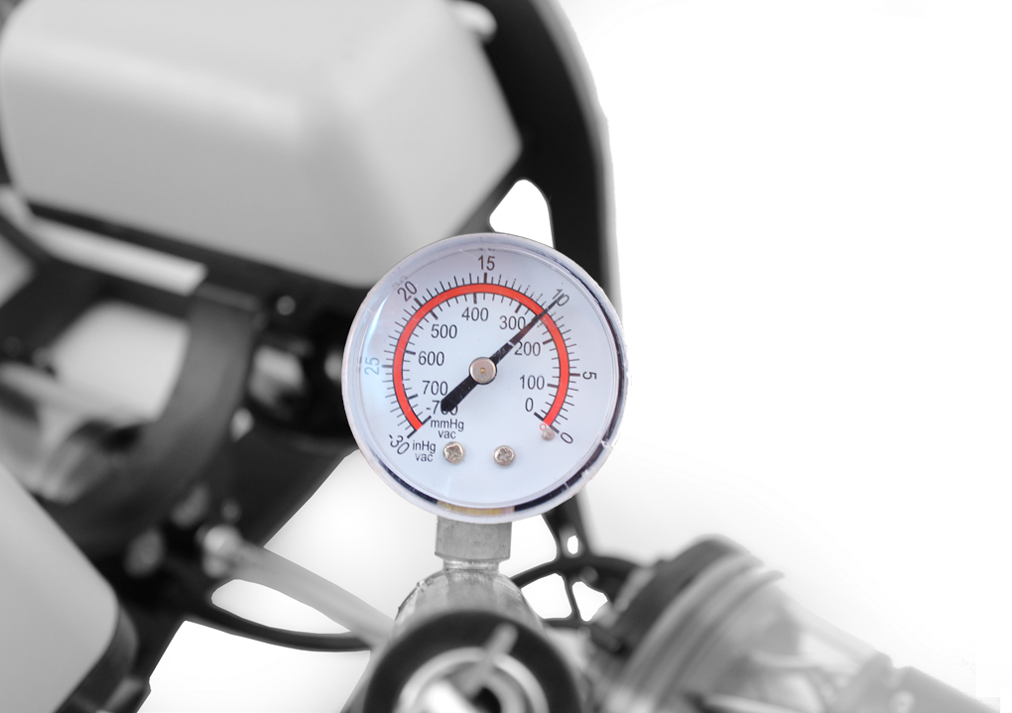
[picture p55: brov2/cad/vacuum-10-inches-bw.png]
	

5. Let the BlueROV2 and pump sit for 15 minutes.

6. If the gauge reads above 9 in. Hg [31 kPa] after 15 minutes, your seals are acceptable.

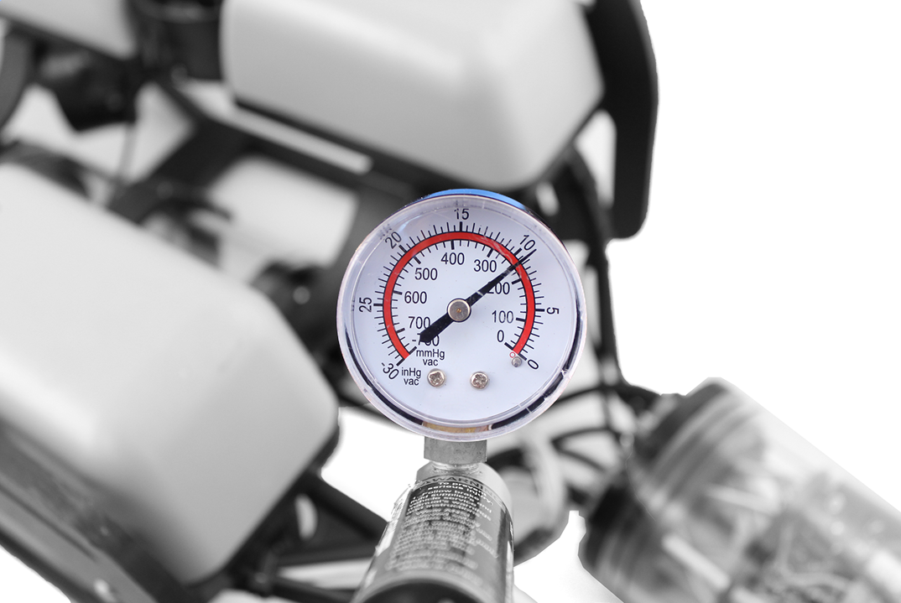
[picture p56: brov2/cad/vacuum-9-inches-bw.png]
	

If the gauge reads below 9 in. Hg [31 kPa] vacuum after 15 minutes, you should check the following:

1. Make sure that the M3 screws on the front and back end caps of the battery and electronics enclosure using the M2.5 hex driver. If you are able to tighten one or more, attempt the vacuum test again.

2. Make sure that the penetrators on the battery and electronics enclosure are fully tightened. Check by attempting to loosen by hand. If you are able to loosen one or more, tighten them then attempt the vacuum test again.

3. Make sure that all of the O-rings are installed in the penetrators. If any are missing, install then attempt the vacuum test again.

4. Check that the face seal O-rings and radial O-rings are installed in the battery and electronics enclosures and in good condition. If you find a damaged or missing O-ring, install and attempt the vacuum test again.

If you are still having trouble holding vacuum, please contact us at <a href="mailto:support@bluerobotics.com">support@bluerobotics.com</a>

To continue assembling the BlueROV2, remove the acrylic tube and dome from the electronics enclosure.

## Installing the Power Wires from the Penetrators

To install the wires from the penetrators you will need the following parts and tools:

- 1 x Large (~#2) Phillips head screw driver

1. Connect the battery power bullet connectors to bullet connectors on XT60 to bullet connector adapter. 

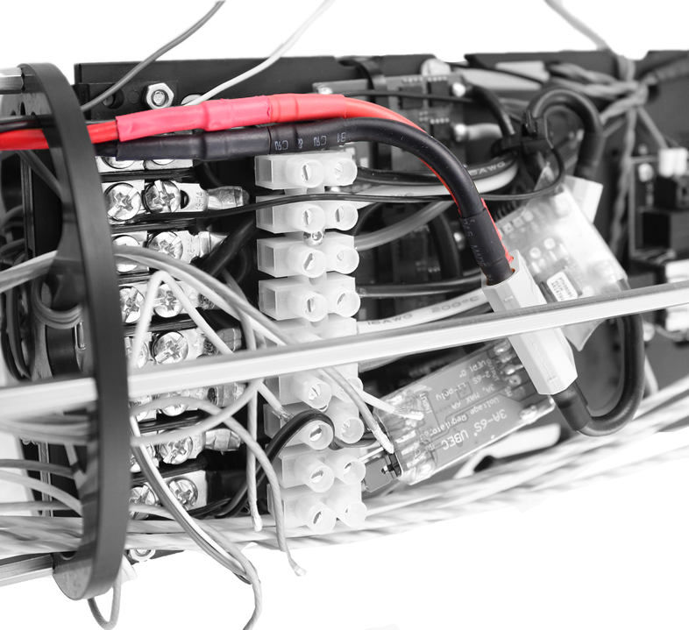
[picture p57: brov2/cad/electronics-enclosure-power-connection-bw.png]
	

2. Connect the Lumen power wire (red) to the Power Terminal Block with the other red wires. Use the rear screw terminal that is second from the bottom. To help keep the cable routing neat, bring the cable through the ESC wires and take out most of the slack.
	
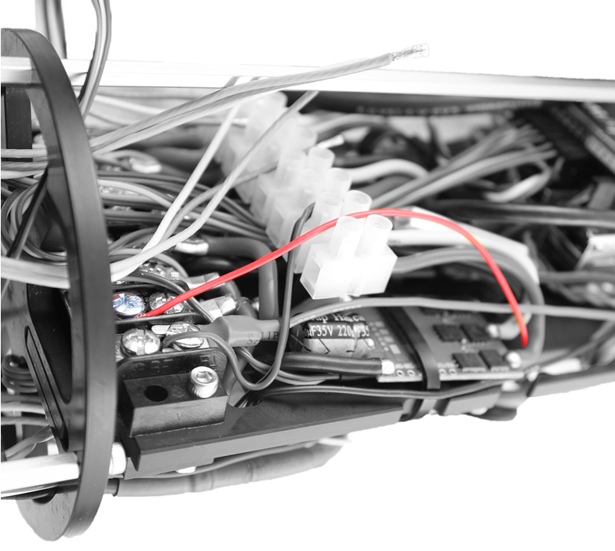
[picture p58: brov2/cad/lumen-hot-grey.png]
	

3. Connect the Lumen ground wire (black) to the Power Terminal Block with the other black wires. Use the rear screw terminal that is second from the bottom. To help keep the cable routing neat, bring the cable through the ESC wires and take out most of the slack.
	
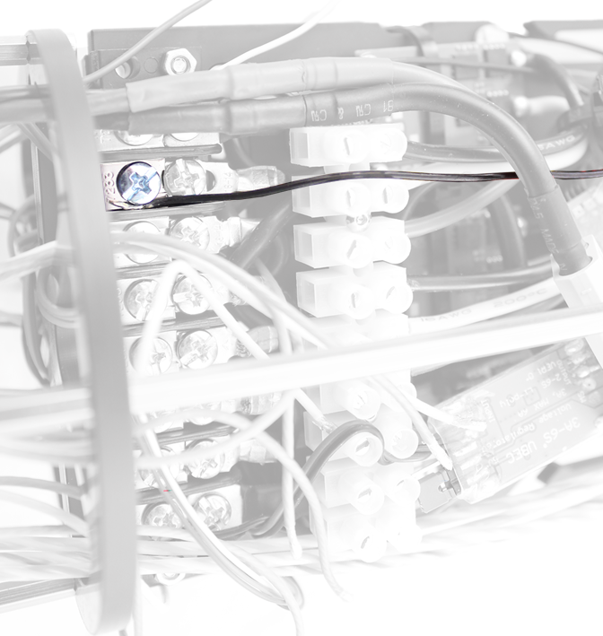
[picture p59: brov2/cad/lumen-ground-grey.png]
	

## Installing the Signal Wires from the Penetrators
	
To install the wires from the penetrators you will need the following parts and tools:

- 1 x Small (~2 mm) flat head screw driver

1. Connect the Lumen signal wire to the Pixhawk channel 7 with the yellow wire oriented toward the bottom of the Pixhawk. 

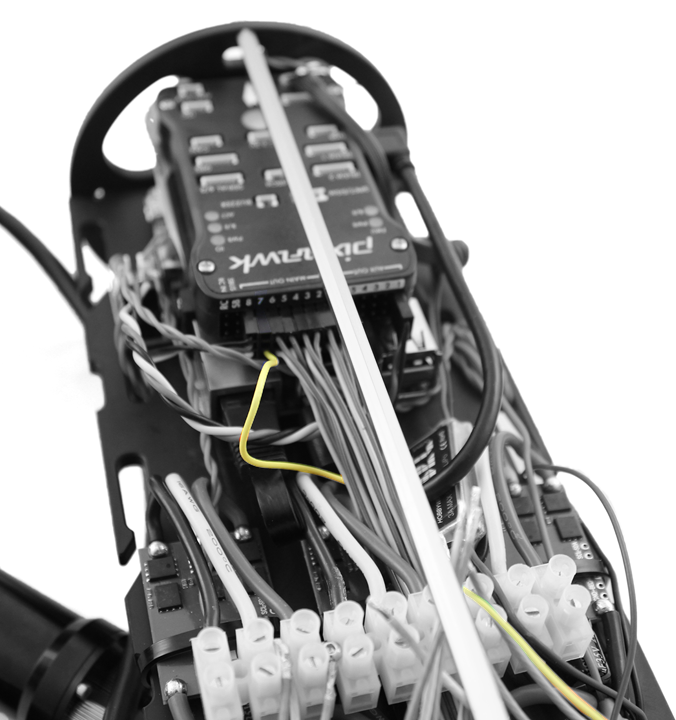
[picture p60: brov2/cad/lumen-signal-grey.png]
	

2. Connect the Bar30 cable to the I<sup>2</sup>C port on the Pixhawk.

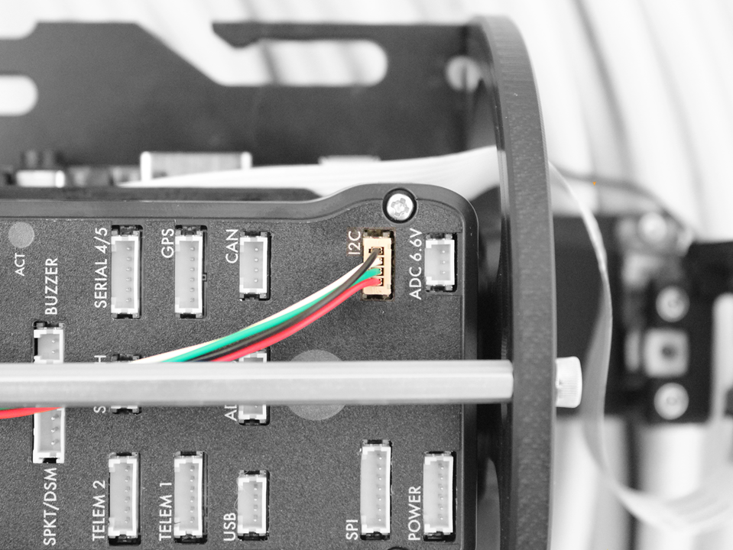
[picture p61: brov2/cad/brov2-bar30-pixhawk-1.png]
	

3. Connect the motor wires to the motor wire terminal block, as shown in the diagrams below.

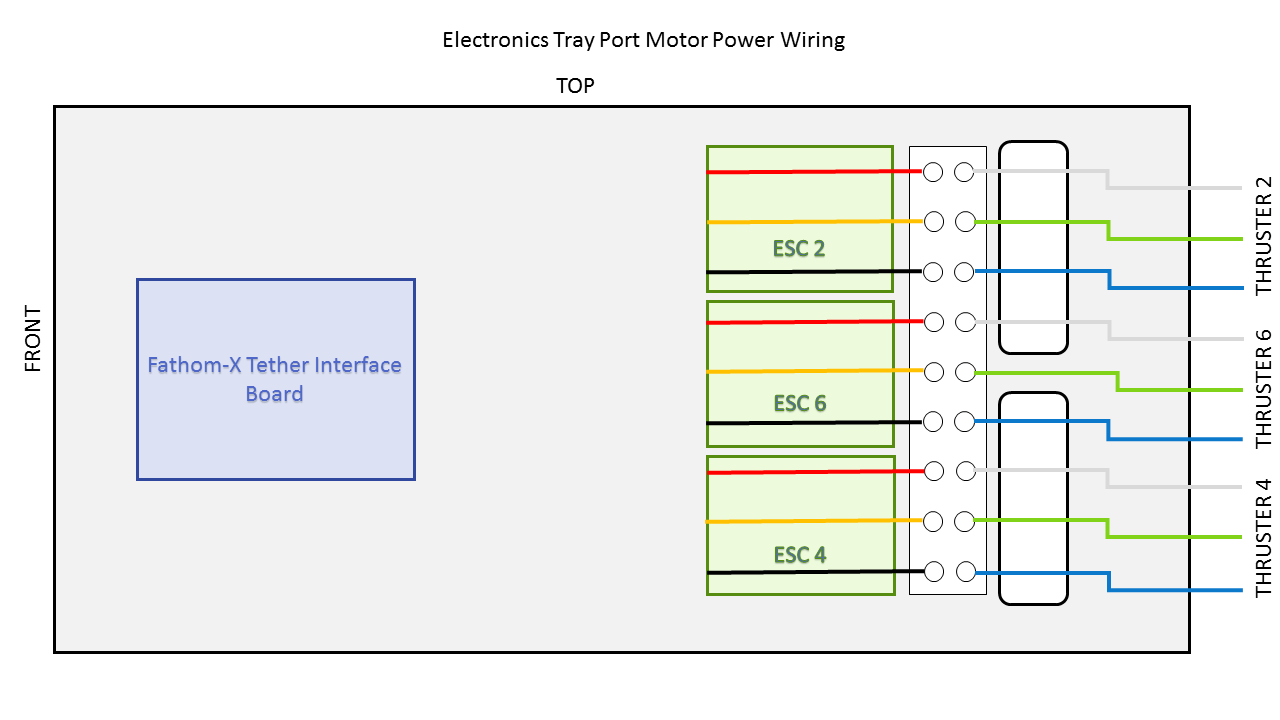
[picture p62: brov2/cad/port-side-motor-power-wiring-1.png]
	

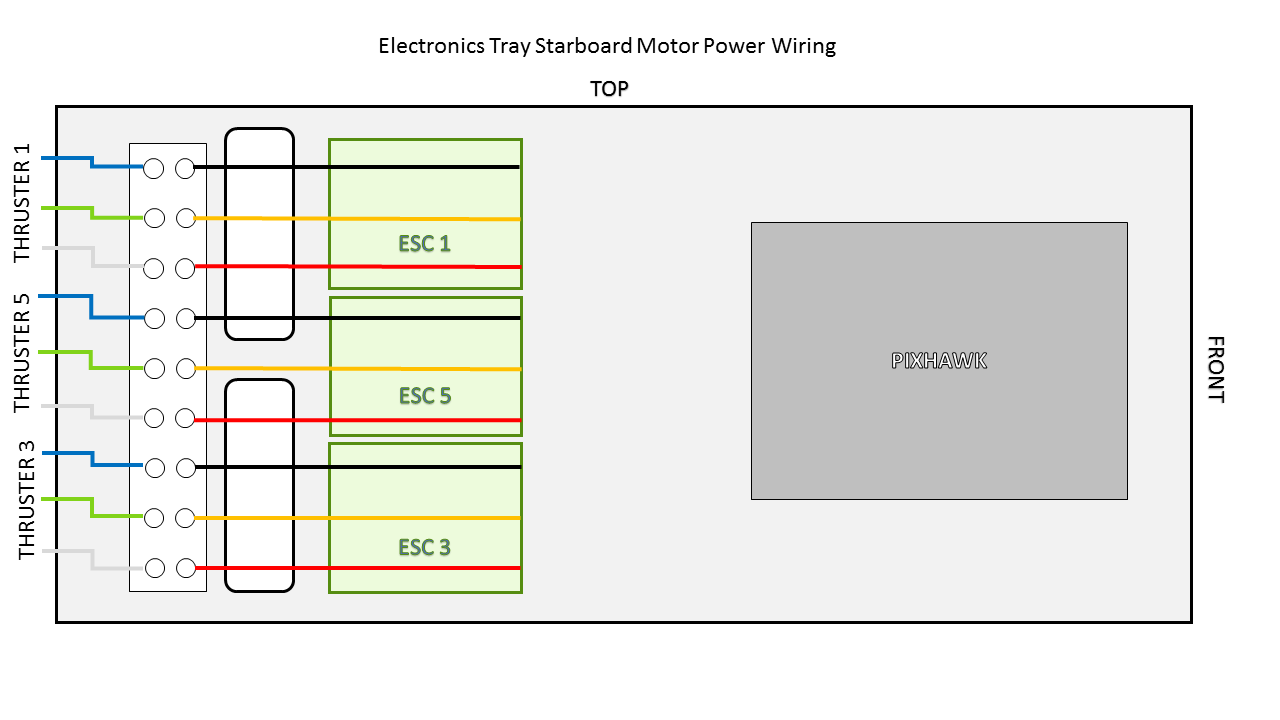
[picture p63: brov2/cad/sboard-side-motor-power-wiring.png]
		
	
4.	Slide the new 3 pole Euro terminal blocks into their mounting location on top of the 9 pole Euro terminal blocks and one of the poles is between the aluminum standoff.

5.	Connect the motor power wires from the thrusters 7 and 8 to the motor terminal blocks as shown, using your 2 mm flat head screw driver.

6.	Connect the motor power wires from the new ESCs to the motor terminal blocks as shown, using your 2 mm flat head screw driver.

7.	Plug ESC Signal Wires into Pixhawk with the following steps:

    - Unplug the Lumen light signal wire from the Pixhawk Channel 7 port and replug it into Aux Channel 1 with the yellow wire oriented toward the bottom of the Pixhawk. 
    - Unplug the camera tilt servo from Pixhawk Channel 8 and replug it into Aux Channel 2 with the yellow signal wire oriented toward the bottom of the Pixhawk.
    - Plug the servo signal wire for Thruster 7 into Channel 7 on the Pixhawk with the white signal wire oriented toward the bottom of the Pixhawk.
    - Plug the servo signal wire for Thruster 8 into Channel 8 on the Pixhawk with the white signal wire oriented toward the bottom of the Pixhawk.

8.	Connect the ESC Power Wires into open screw terminals on the respective positive and negative terminal blocks.
	
9. Connect the tether wires to the Fathom-X Tether Interface Board. The other 6 wires can do not need to be connected to anything the operate the ROV. They are for future expansion.

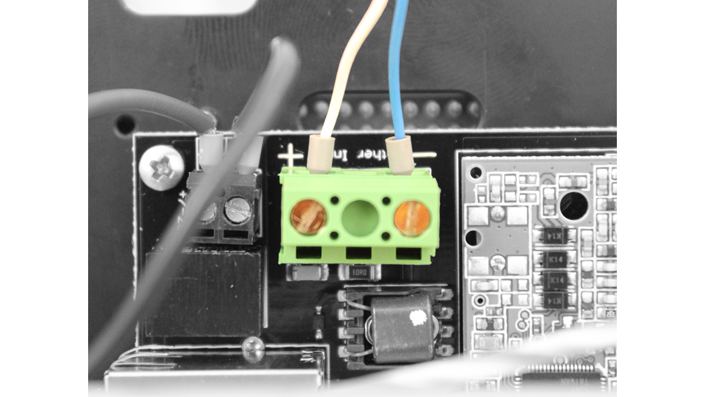
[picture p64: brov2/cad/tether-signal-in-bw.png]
	

## Cable Routing

To route the cables in the Electronics Enclosure so that they will not snag on the Watertight Enclosure for ROV/AUV (4" Series) with Dome End Cap installed you will need the following parts and tools:

- 3 x 5 1/2" zip ties
- 1 x Wire strippers or scissors

1. On the starboard side (Pixhawk side) collect the Bar30 wires and the Lumen signal wire and zip tie them to the long hex standoff slightly forward of the Motor Terminal Block using one zip tie. Make sure that the locking head of the zip tie and the wires are oriented to the inside of the long hex standoff.

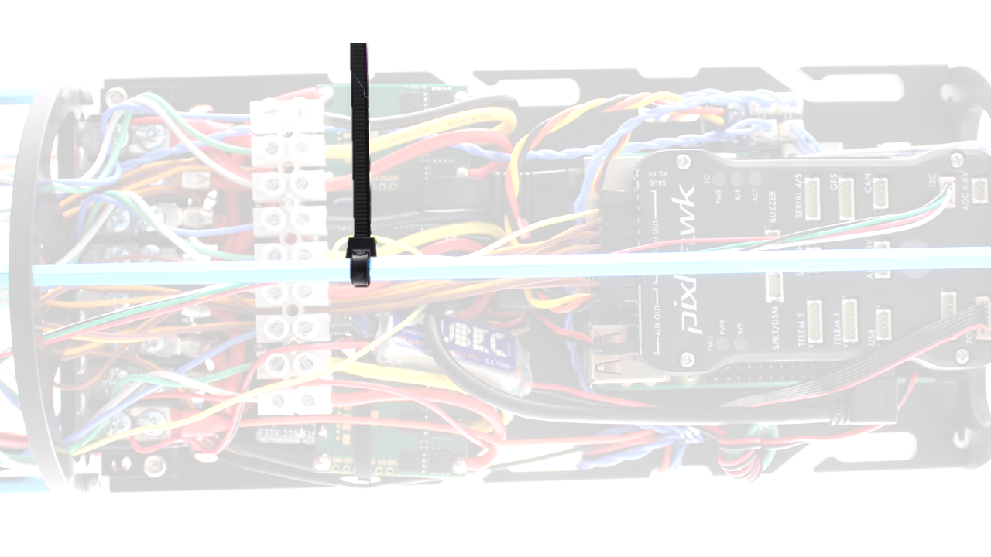
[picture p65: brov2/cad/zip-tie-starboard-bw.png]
	

2. On the port side (Fathom-X Tether Interface Board side) collect the Fathom Tether wires and zip tie them to the long hex standoff approximately even with the back of the Fathom-X Tether Interface Board and approximately even with the Motor Terminal Block. Make sure that the locking heads of the zip ties and the wires are oriented to the inside of the long hex standoff. 

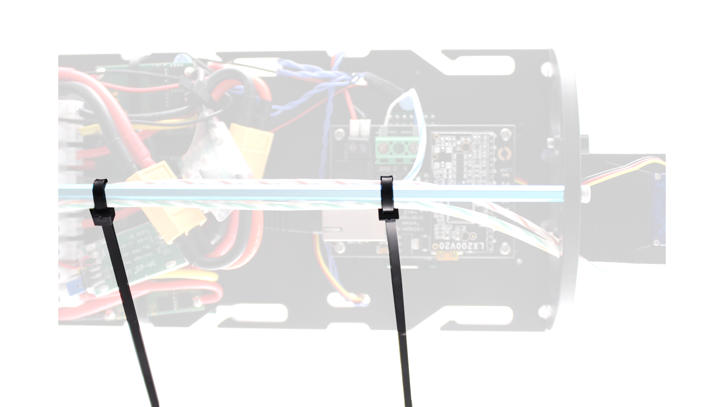
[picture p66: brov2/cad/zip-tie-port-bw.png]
	

# Final Assembly

## Adding Desiccant to the Electronics Enclosure

If you ordered your BlueROV2 prior to February 14, 2018 you will need to order [Moisture Indicating Silica Gel Desiccant](https://bluerobotics.com/store/tools/desiccant-r1/) in order to complete this step. This step is optional, but it will improve the usability of the BlueROV2, especially if you are planning on operating your ROV in humid environments with cold water.

The desiccant will absorb humidity that is inside of the Electronics Enclosure to prevent the dome from fogging up during dives. It will turn pink as it absorbs humidity.

1. Fill one of the Desiccant Bags with Moisture Indicating Silica Gel Desiccant and close the draw string. Make sure that you close the lid of the Moisture indicating Silica Gel Desiccant after you have filled the bag. It will become saturated in about a day if left open to air. 



2. Install the desiccant bag near the Fathom-X Tether Interface. This step will have to be combined with installing the Watertight Enclosure (4" Series) over the Electronics Tray since the bag will be "floating" inside of the enclosure

[Pictures Coming Soon]

## Mounting the Electronics Enclosure onto the Frame

To mount the Electronics Enclosure to the frame you need the following parts and tools:

- 1 x Watertight Enclosure for ROV/AUV (4" Series) with Dome End Cap installed
- 1 x Threadlocker
- 1 x Bag with four M3x16 screws
- 1 x 2.5 mm hex driver

1. Apply silicone grease to the two radial O-rings on the O-Ring Flange (4" Series) that is attached to the Electronics Tray then install the Watertight Enclosure (4" Series) with installed Dome End Cap to the O-Ring Flange (4" Series). 

2. Apply one drop of threadlocker to each of the four M3x16 screws. Roll the screws around on a paper towel to evenly spread the threadlocker and to remove excess threadlocker.

3. Mount the Electronics Enclosure to the frame using the M3x16 screws so that the dome is on the same side as the front center panels (the center panels _without_ the 3 large holes). Install the M3x16 screws through the clips and into the Enclosure Cradle (4" Series). It is easier to install these screws if the clips are not fully tightened until all screws are through the clips and threading into the Enclosure Cradle (4" Series). This allows to clips to rotate so you can find the threaded hole in the Enclosure Cradle (4" Series) easily. 

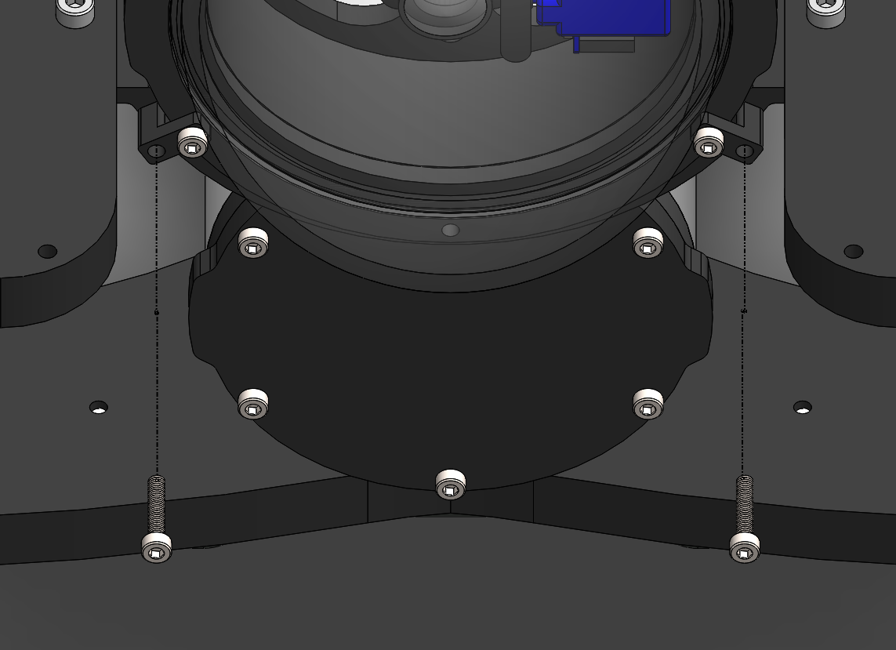
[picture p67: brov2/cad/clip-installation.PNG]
	

## Mounting the Thrusters to the Frame

To mount the thrusters to the frame, you need the following parts and tools:

- 1 x 2.5 mm hex driver
- 3 x T200 Thruster with Clockwise Propeller installed
- 3 x T200 Thruster with Counter-Clockwise Propeller installed
- 1 x Bag with 16 M3x16 screws and 8 M3x12 screws in smaller bag
- 1 x Assembled ROV frame

The horizontal thrusters have two mounting options. One is at a 45° angle to forward, and the other is at a 30° angle to forward. The thrusters mounted at 45° will give you equal thrust in all directions. Mounting the thrusters at 30° will give you 25% more forward thrust in exchange for 25% less thrust in strafing. To mount the thrusters at 45° use the holes shown in the picture below. The hole with the asterisk is the hole that should be closest to the nose cone on the thruster.

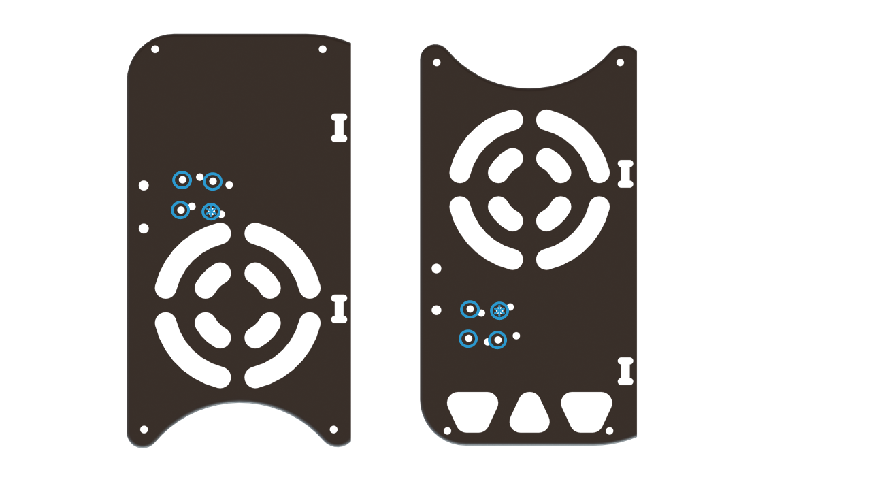
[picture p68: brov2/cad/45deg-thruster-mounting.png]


To mount the thrusters at 30° use the holes shown in the pictures below. The hole with the asterisk is the hole that should be closest to the nose cone on the thruster.

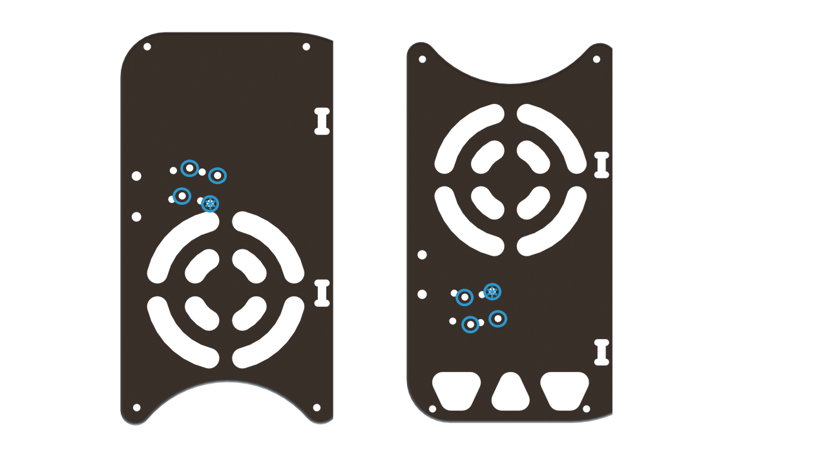
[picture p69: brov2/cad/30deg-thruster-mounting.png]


For the sake of clarity, the hole with the asterisk on the thruster shown below is the hole that is closest to the nose cone.

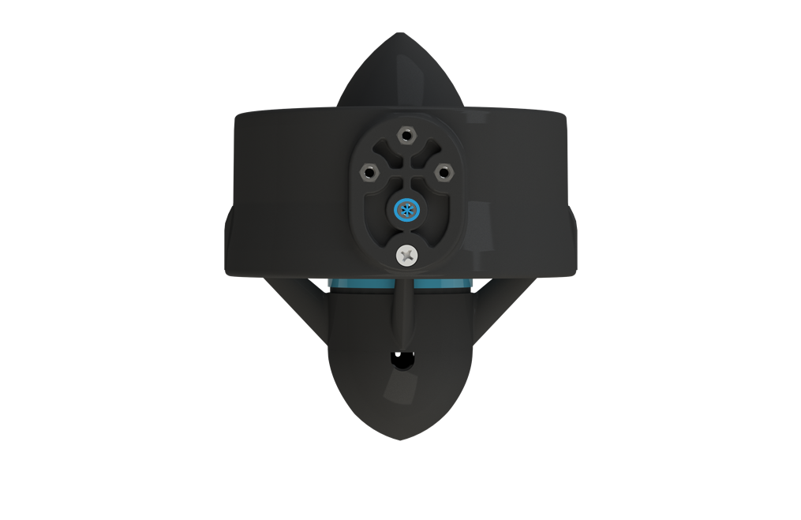
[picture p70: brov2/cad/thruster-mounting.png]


Here is a diagram of where the thrusters go, and how they should be oriented. The green thrusters should have counter-clockwise propellers and blue thrusters should have clockwise propellers. The order of installation matters here. You cannot get the front thrusters on if the rear ones were installed first.

<p align="center">

</p>

1. Apply one drop of threadlocker to the 16 M3x16 screws and the 8 M3x12 screws. Roll the screws around on a paper towel to evenly spread the threadlocker and to remove excess threadlocker.

1. Install thrusters 1 and 2 underneath the front center panels, using the M3x16 screws. Tighten the screws so that they indent the frame slightly. It is physically possible to keep turning the screw at this point, but it isn't recommended.
	
3.	Install thrusters 5, 6, 7 and 8, using the M3x12 screws on the outside of the side panels. Tighten the screws so that they indent the frame slightly.

3. Install thrusters 3 and 4 underneath the rear center panels, using the M3x16 screws. Tighten the screws so that they indent the frame slightly.

## Install New Thruster Guards

To install the new thruster guards, you will need the following parts and tools:

-	1 Bag of 12 M4x16mm screws
-	1 Bag of #4x3/8” Thread forming screws
-	8 x Heavy Guard Mounting Brackets
-	2 x Heavy Guards
-	1 x Threadlocker
-	1x #1 Phillips head screwdriver

1. Apply one drop of threadlocker to each of the M4x16mm screws. Roll the screws around on a paper towel to evenly spread the threadlocker and to remove excess threadlocker.

2. Install 4 of the thruster guard mounting brackets on the outside of the frame using 4 M4x16 screws as shown below.

3. Place the new thruster guards on the brackets you had previously installed and make sure the holes align. The thruster guards only install in one direction with the shorter leading edge of the guard oriented towards the front end of the vehicle. Secure the guards to the brackets using 4 M4x16 screws.

4. Install four more thruster guard mounting brackets (two on each side) in the holes near the middle of the ROV using one M4x16 screw and one #4x3/8” thread forming screw per bracket.

4. Tighten all the screws evenly until they are tight enough to properly secure the thruster guard to the frame and there is no excess freedom of movement.

## Mounting the Lights

To install the Lumen mounts you will need the following parts and tools:

- 1 x Bag with the Lumen mounts, O-rings, and four M3x12 socket head cap screws 
- 1 x 2.5 mm hex driver 
- 1 x BlueROV2 frame
- 1 x Threadlocker

1. Apply one drop of threadlocker to each of the M3x12 screws. Roll the screws around on a paper towel to evenly spread the threadlocker and to remove excess threadlocker.

2. Install the mounts. Make sure not to overtighten the screw that goes into the slot. Only tighten it so that it slightly indents the frame. 

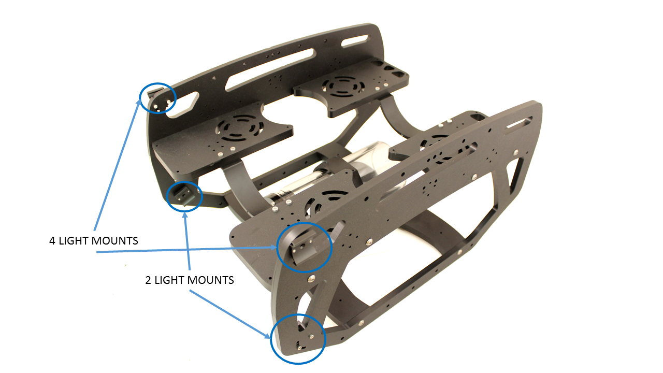
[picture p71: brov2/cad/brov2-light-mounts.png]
	
	
3. Loop one of the size 133 O-rings from the bag that had the Lumen Mounts and screws around each Lumen Mount and Lumen as shown below.

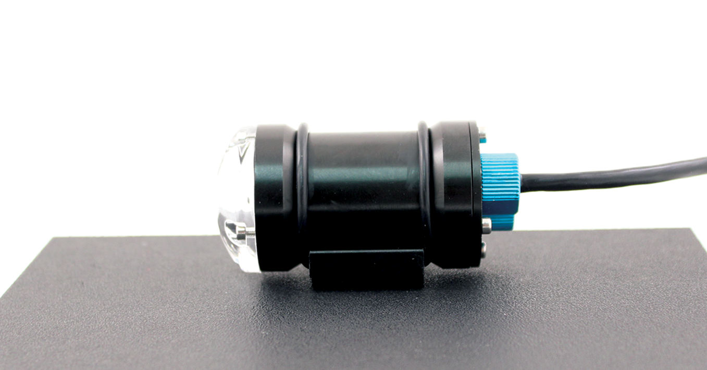
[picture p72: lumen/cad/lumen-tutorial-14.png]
	

## Mounting the Tether to the Frame

The tether needs to be firmly mounted to the frame to prevent the tether penetrator from being loosened through normal use. To do this, you will need the following parts and tools:

- 1 x Bag with thimble and 5 large zip ties
- 1 x Fathom Tether 
- 1 BlueROV2 frame

1. Loop the tether around the plastic thimble at a point about 12 inches (30 cm) away from the tether penetrator.
	
2. Firmly attach 3 of the zip ties, alternating directions as they are installed, around the tether right where it enters and exits the thimble. Hold the tether firmly in place against the thimble until it is secured.

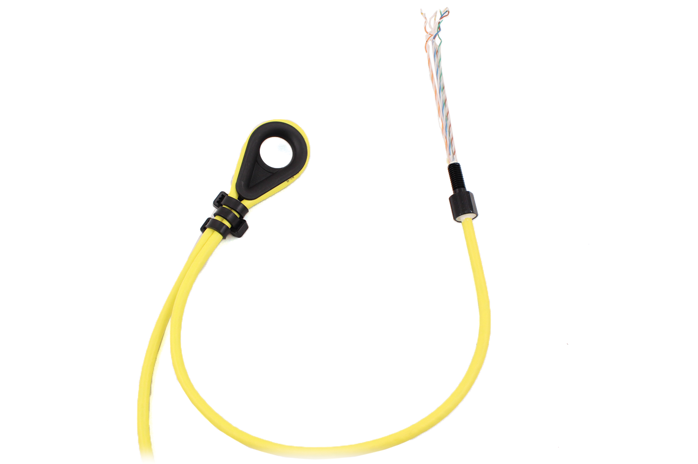
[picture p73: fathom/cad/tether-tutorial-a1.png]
		
	
3. Attach the thimble to the rear panel as shown

		
	
## Thruster and Lumen Cable Management

To clean up the thruster and lumen wires, you will need the bag of 30 zip ties and your scissors/wire cutters. 

The primary goal of Thruster and Lumen cable management is to prevent the wires from getting cut by the propellers. Make sure to check that no wire can reach a propeller after you have finished routing the cables. Below are some examples of what the cable routing should look like.







## Installing the Fairings and Buoyancy

The buoyancy comes preinstalled in the fairings, but make sure it is still in all of the fairings prior to installing the fairings. To install the fairings, you will need the following parts and tools:

- 4 x Fairings with buoyancy installed 
- 1 x Bag with 16 self tapping screws 
- 2 x Heavy additional buoyancy blocks
- 2 x Heavy fairings
- 1 x Bag of 4 fairing screws
- 1 x \#1 Phillips head screwdriver 

1. Remove the Lumens from their mount. You only need to remove the lower two Lumens from their mount if you have four.

	

2. Install the screws through the center panels and into the fairings.
	
	
	
3.	Place the new round Heavy buoyancy blocks into the open space where Thrusters 5 and 6 used to be. Ensure the flat sides of the blocks are parallel to the sides of the ROV.

4.	Place the new plastic Heavy fairings on top of the buoyancy blocks and secure them to the old fairing blocks using the included self-tapping fairing screws.
	
5. Reinstall the Lumens.

	

## Mounting Ballast to the Frame

To mount the ballast to the frame you need the following parts and tools:

- 10 x 200g ballast weights
- 10 x 8-16 Thread, 5/8" Long, Thread-Forming Screw   
- 1 x \#2 Phillips head screwdriver

To get the longest battery life and the best driving experience, it is important to have the ROV close to balanced from front to back in water and close to neutrally buoyant. Trimming the ballast may involve a bit of trial and error. The pictures below should provide a good starting point for mounting ballast if you have a stock BlueROV2 with the [recommended battery.](https://bluerobotics.com/store/rov/bluerov2/battery-li-4s-18ah-r1/)

<b> <font size="4"> BlueROV2 with 2 <i> Lumen </i> Lights </font> </b> 
<p align="center">

</p>

<b> <font size="4"> BlueROV2 with 4 <i> Lumen </i> Lights </font> </b> 
<p align="center">

</p>

# Topside Setup 

To get your topside ready to connect to the BlueROV2 you will need the following parts and tools:

- 1 x Fathom-X Tether Interface Board
- 1 x 2 mm flat head screw driver
- 1 x Computer (Mac, Windows, Linux)
- 1 x Ethernet cable 
- 1 x USB to Ethernet adapter (if your computer does not have an Ethernet Port)
- 1 x Mini-USB cable

1. Connect the Fathom Tether to the Fathom-X Tether Interface Board. 

2. Connect the Ethernet port of the Fathom-X Tether Interface Board to you computer. If you do not have an Ethernet port on you computer connect the Ethernet port on the Fathom-X Tether Interface Board to a USB to Ethernet adapter then connect the adapter to your computer.

3. Connect your Mini-USB the the Fathom-X Tether Interface Board and to a USB power supply that can supply at least 500 milliamps. Most computer USB ports can do this, but if the "Link" LED does not light up try using a USB charger.



# Next Steps

First, set up the software on your topside computer. Please see our [Software Setup](/brov2/software-setup/) page.

Next, refer to the [Operating Manual](/brov2/operation/) to learn how complete your first dive.

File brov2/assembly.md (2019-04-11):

---
layout: default
title: BlueROV2 Assembly
permalink: /brov2/assembly/
order: 1
topnavbar: brov2
nav:
- Archived Instructions: archived-assembly-instructions
- Introduction: assembly-intro
- - Safety: safety
- Required Tools: required-tools-not-included
- Frame Assembly: assembling-the-frame
- - Battery Enclosure: mounting-the-battery-enclosure-to-the-bottom-panel
- - Center Panels: assembling-the-center-panels
- - Frame: assembling-the-frame-1
- Electronics Overview: electronics-enclosure-overview
- - Connection diagrams: connection-diagrams
- Cable Installation: installing-the-cables
- - Removing Endcap: removing-the-electronics-enclosure-endcap
- - Penetrator Installation: installing-the-penetrators
- - End Cap Installation: installing-the-end-cap
- - Finishing Battery Enclosure: finishing-the-battery-enclosure
- - Optional Preliminary Vacuum Test: optional-preliminary-vacuum-test
- - Penetrator Power Wiring: installing-the-power-wires-from-the-penetrators
- - Penetrator Signal Wiring: installing-the-signal-wires-from-the-penetrators
- - Cable Routing: cable-routing
- Final Assembly: final-assembly
- - Desiccant: adding-desiccant-to-the-electronics-enclosure
- - Mounting Electronics Enclosure: mounting-the-electronics-enclosure-onto-the-frame
- - Mounting Thrusters: mounting-the-thrusters-to-the-frame
- - Mounting Lights: mounting-the-lights
- - Mounting the Tether: mounting-the-tether-to-the-frame
- - External Cable Management: thruster-and-lumen-cable-management
- - Installing Fairings: installing-the-fairings-and-buoyancy
- - Ballast: mounting-ballast-to-the-frame
- Topside Setup: topside-setup
- Next Steps: next-steps

store-links:
- BlueROV2: https://bluerobotics.com/store/rov/bluerov2/bluerov2/

manual-links:
- Software Setup: /brov2/software-setup/
- Operations Manual: /brov2/operation/

redirect: https://bluerobotics.com/learn/bluerov2-assembly/
---



# Archived Assembly Instructions

These are the most recent assembly instructions. Depending on the age of your kit, you may wish to refer to an older version:

- [Assembly Instructions for Kits Shipped Prior to March 2017](/brov2/assembly-pre201703/)

# Assembly Intro

The BlueROV2 kit comes almost ready to dive. The assembly can be completed with basic hand tools; no soldering or potting is required. We have included a couple of the tools to make assembly and regular use as easy as possible.

## Safety 

<i class="fa fa-exclamation-triangle fa-fw fa-2x text-warning"></i> When working with electricity, especially in water, always practice caution. Always ensure that connections are secure and watertight. Keep your body away from spinning motors and propellers.

<i class="fa fa-exclamation-triangle fa-fw fa-2x text-warning"></i> When working with silicone grease and threadlocker, take care to minimize skin contact. Wear protective nitrile or PVC gloves when handling.

<i class="fa fa-exclamation-triangle fa-fw fa-2x text-warning"></i> Only apply threadlocker to screws contacting metal or the HDPE frame. Most threadlockers are not chemically compatible with with polycarbonate, and will damage the thrusters, fairings, and dome flange if used here. Refer to the documentation and chemical compatibility notes of your threadlocker of choice for more information.

# Required Tools (Not Included)

- \#2 Phillips head screwdriver 
- Wire cutters or scissors (for cutting zip ties)
- Medium-strength (blue) threadlocker such as [Loctite 243](https://www.amazon.com/Loctite-1330799-Resistant-thread-locker-6-milliliter/dp/B004L439FE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)
- Isopropyl alcohol or isopropyl alcohol wipes
- 2 mm flat head screw driver

# Assembling the Frame

## Mounting the Battery Enclosure to the Bottom Panel

To mount the battery enclosure to the bottom panel you will need the following parts and tools:

- 2 x Enclosure Clamp (3" Series)
- 1 x Threadlocker 
- 1 x Bottom panel 
- 1 x Bag with four M4x14 socket head cap screws and four M3x12 socket head cap screws
- 1 x Watertight Enclosure for ROV/AUV (3" Series)
- 1 x 3 mm hex key
- 1 x 2.5 mm hex driver

1. Remove the Aluminum End Cap with 4 Holes (3" Series) to open the Watertight Enclosure for ROV/AUV (3" Series) and set the bags inside of it to the side, except for the bag with four M4x14 and four M3x12 screws in it.

2. Apply one drop of threadlocker to the bottom of each M4x14 socket head cap screw. Roll the screws around on a paper towel to evenly spread the threadlocker and to remove excess threadlocker.

	

3. Attach one of the Enclosure Clamps (3" Series) to the bottom panel using the four M4x14 socket head cap screws. Be sure that the screw head is in the [counterbore](https://en.wikipedia.org/wiki/Counterbore). The bottom panel is only counterbored on one side. Tighten the screws until you can feel them start to dig into the bottom panel.

	 

4. Apply one drop of threadlocker to each of the 4 M3x12 screws. Roll the screws around on a paper towel to evenly spread the threadlocker and to remove excess threadlocker.

6. Place the Watertight Enclosure for ROV/AUV (3" Series) between the two Enclosure Clamps (3" Series). The Enclosure Clamps have tapped holes on one side and untapped holes on the other. 

<i class="fa fa-exclamation-triangle fa-fw fa-2x text-warning"></i> Ensure NO threadlocker comes into contact with the acrylic tube.

Install the four M3x12 screws into the Enclosure Clamps (3" Series) so that the screws pass through the untapped holes on the first clamp and are secured into the tapped holes on the alternate clamp. Install all four screws loosely at first and then slowly tighten them on both sides evenly. Take care not to overtighten the screws. Keep the battery enclosure approximately centered in the Enclosure Clamps (3" Series).



When you are finished tightening the screws, both sides should look similar to this.


	
## Assembling the Center Panels

To assemble the center panels you will need the following parts and tools:

- 2 x Enclosure Cradle (4" Series)
- 2 x Front center panels 
- 2 x Rear center panels 
- 1 x Threadlocker 
- 1 x Bag with eight M4x18 socket head cap screws 
- 1 x 3 mm hex key 

1. Apply one drop of threadlocker to each of the eight M4x18 screws. Roll the screws around on a paper towel to evenly spread the threadlocker and to remove excess threadlocker.

2. Attach one of the Enclosure Cradle (4" Series) to the rear center panels. Tighten the screws until they indent the rear center panels slightly. 

	
	
3. Attach the other Enclosure Cradle (4" Series) to the front center panels. Tighten the screws until they indent the front center panels slightly. 

	
	
## Assembling the Frame

To assemble the frame you will need the following parts and tools:

- 1 x Threadlocker 
- 1 x Bag with 12 M5x16 button head cap screws 
- 2 x Side panels
- 1 x Bottom panel with the Watertight Enclosure for ROV/AUV (3" Series) installed
- 1 x Front center panel assembly
- 1 x Rear center panel assembly
- 1 x 3 mm hex key

1. Apply one drop of threadlocker to each of the 12 M5x16 screws. Roll the screws around on a paper towel to evenly spread the threadlocker and to remove excess threadlocker.
	
2. Install both side panels to the bottom panel using four of the M5x16 screws; the Aluminum End Cap (3" Series) on the Watertight Enclosure for ROV/AUV (3" Series) should be on the same side as the Lumen mounting holes. **It is very important to avoid overtightening these screws.** Tighten these screws using the provided 3 mm hex key. Hold the short end of the 3 mm hex key while you are tightening the M5x16 screws. Do not tighten beyond the tightness you can achieve holding the short end of the 3 mm hex key. 

	
	
3. Install the center panel assemblies to the side panels using the remaining eight M5x16 screws. **It is very important to avoid overtightening these screws.** Tighten these screws using the provided 3 mm hex key. Hold the short end of the 3 mm hex key while you are tightening the M5x16 screws. Do not tighten beyond the tightness you can achieve holding the short end of the 3 mm hex key.

	
	
Now the BlueROV2 should look like the picture below. 



# Electronics Enclosure Overview

The images below show orientation of the main pieces of hardware in the electronics enclosure. They also point out the names of several of the important parts for assembly that will be discussed in the remaining instrustions.

<b> <font size="4"> Top View </font> </b> 


<b> <font size="4"> Starboard View </font> </b> 


<b> <font size="4"> Port View </font> </b> 


<b> <font size="4"> Front View </font> </b> 


## Connection diagrams

These diagrams outline all of the electrical connections between components in the ROV. There is a different diagram for each version of the ROV that Blue Robotics has produced.

- [BlueROV2 with red-wire (BEC) ESCs](/brov2/cad/connections/BlueROV2_bec.pdf) (Pre-2018)
- [BlueROV2 with no-red-wire ESCs](/brov2/cad/connections/BlueROV2_no_bec.pdf) (2018 and later)
- [BlueROV2 Heavy](/brov2/cad/connections/BlueROV2_heavy.pdf)

# Installing the Cables 

## Removing the Electronics Enclosure Endcap

The endcap will need to be removed from the electronics enclosure in order to install the cable penetrators. To remove the endcap you will need the following parts and tools:

- 1 x Large flat head screw driver (Optional)
- 1 x The electronics enclosure assembly
- 1 x 2.5 mm key driver 

1. Remove the Watertight Enclosure for ROV/AUV with Dome End Cap installed from the rear O-Ring Flange (4" Series). If this step is difficult, you can place a large flat head screwdriver into the slots on the O-Ring Flange (4" Series), and then twist to get a gap between the acrylic tube and the O-Ring Flange (4" Series). Once you have the gap, you can wedge a screw driver between the end of the acrylic tube and the O-Ring Flange (4" Series) to finish removing the acrylic tube.

	
		
2. Remove the Aluminum End Cap with 14 Holes by removing the six M3x12 screws using the M2.5 hex driver. Place the M3x12 screws, clips (small L-shaped parts), and face seal O-ring in a safe place. 

	

## Installing the Penetrators

To install the Penetrators you will need the following parts and tools:

- 1 x Cable Penetrator Nut (Black for Standadrd Tether/Red for Slim Tether), and O-ring from one end of the Tether
- 6 x Cable Penetrator Nut (red), and O-ring from bag inside each Thruster tube packages
- (Optional if no Lumens) 1 x Cable Penetrator Nut (red) and O-ring from spares bag
- 1 x Silicone Grease - 10g Tube
- 1 x Aluminum End Cap with 14 Holes w/ 3 Cable Penetrator Blanks, 1 Bar30 Pressure Sensor, 1 Enclosure Vent and Plug, and 1 power cable installed
- 3 x T200 with counter-clockwise thrusters 
- 3 x T200 with clockwise thrusters 
- 1 x Set of Lumen lights (optional)
- 1 x Fathom ROV Tether
- 1 x Penetrator Wrench

The Aluminum End Cap with 14 Holes comes with 3 Cable Penetrator Blanks, 1 Bar30 Pressure Sensor, 1 Enclosure Vent and Plug, and 1 power cable installed.



If you install the remaining penetrators as shown in the diagram below, it will keep everything neat and organized.


	
1. Remove eight of the O-rings and apply silicone grease to them. Keep the other O-ring in the bag, you will need it in a minute.

	

2. Wipe the exterior surface of the electronics enclosure endcap clean with isopropyl alcohol or isopropyl alcohol wipes, and make sure it is free of any particles in the areas where the penetrator O-rings will sit.

3. Install the O-rings onto all of the thruster penetrators, the lumen penetrator, and the tether penetrator. 

4. Install the penetrators to the end cap in the order shown below. Tighten to finger tight, then use the provided wrench to tighten them an additional ~1/16 of a turn. If you can't loosen them with your fingers, they are tight enough. 

	1. Thruster 1 (CCW propeller) with red penetrator nut
	2. Thruster 5 (CCW propeller) with red penetrator nut
	3. Thruster 3 (CW propeller) with red penetrator nut
	4. Lumen with red penetrator nut (or Blank Penetrator (red) if not installing Lumens)
	5. Thruster 4 (CW propeller) with red penetrator nut
	6. Thruster 6 (CW propeller) with red penetrator nut
	7. Thruster 2 (CCW propeller) with red penetrator nut
	8. Tether with black penetrator nut (standard Tether) or red penetrator nut (Slim Tether)

## Installing the End Cap

To reinstall the Aluminum End Cap with 14 Holes you will need the following parts and tools:

- The face seal O-ring, the 6 M3x12 screws, and the clips that you removed from the end cap earlier
- 1 x Silicone Grease - 10g Tube
- 1 x Aluminum End Cap with 14 Holes with all Cable Penetrators and Blank Penetrators installed
- 1 x 2.5 mm hex driver

1. Clean the O-ring and make sure that it is free of any debris or damage. 

2. Clean the O-Ring Flange (4" Series) and make sure that the O-ring groove is free of any debris or damage.

3. Apply Silicone grease to the O-ring.

4. Install face seal O-ring onto the O-Ring Flange (4" Series). 

5. Apply one drop of threadlocker to each of the M3x12 screws. Roll the screws around on a paper towel to evenly spread the threadlocker and to remove excess threadlocker.
	
6. Install Aluminum End Cap with 14 Holes with all Cable Penetrators and Blank Penetrators installed onto the O-Ring Flange (4" Series). Do not fully tighten any screws when first installing them; it may cause the O-ring to slip out of its groove. The end cap's orientation when installed should match the image below. Make sure that the clips are oriented correctly. One should be just right of the Thruster 3 penetrator, and the other should be just left of the Thruster 4 penetrator. 

	

## Finishing the Battery Enclosure

To complete the assembly of the battery enclosure you need the following parts and tools:

- 1 x Bag labeled "Extra Blank Penetrators [2]"
- 1 x Silicone Grease - 10g Tube
- 1 x End Cap with 4 Holes (3" Series)
- 1 x Penetrator wrench
- 1 x XT90 to 3.5 mm bullet connector adapter
- 1 x 1.5 inch piece of heat shrink
- 1 x Heat gun, hairdryer, or lighter

1. Apply silicone grease to the O-ring.

2. Install the O-ring onto the battery power cable penetrator.
	
3. Install the battery power cable penetrator into the opening in the battery end cap.

4. Install one Cable Penetrator Nut (Red) on to the battery power cable penetrator and tighten with penetrator wrench.

5. Place the 1.5 inch long piece of black heat shrink over the end of the battery power cable penetrator. 

6. Apply heat to the heat shrink using your heat gun, hairdryer, or lighter until the heat shrink is firmly attached to the penetrator and snug to the two wires. You should be able to see the threads in the penetrator through the heat shrink.

	

7. Install the XT90 to bullet connector adapter to the battery power wire. 

	

8. If you wish to do the Optional Preliminary Vacuum Test, remove the Vent Plug from the Vent Penetrator Bolt and install the endcap onto the battery enclosure. You will also need to remove the Vent Plug for the Vent Penetrator Bolt on the electronics enclosure.

## Optional Preliminary Vacuum Test

This is the best point in the assembly process to perform a vacuum test. Since you have installed all of the penetrators, but have not done any of the wiring, troubleshooting will be as easy as possible. You will need to use the vacuum pump that comes with the kit.

1. Install the Watertight Enclosure (4" Series) with installed Dome onto the O-Ring Flange (4" Series) that is attached to the Aluminum End Cap with 14 Holes (4" Series)

	

2. Assemble the vacuum tee.

	

Now you are ready to perform the preliminary vacuum test.

1. Test your vacuum pump to ensure that it is not leaking. See our [Testing the Test Setup Tutorial](http://docs.bluerobotics.com/tutorials/vacuum-test-plug/#testing-the-test-setup) for detailed instructions. 

2. Insert one of the vacuum plugs into the battery enclosure vent penetrator.

	

3. Insert the other vacuum plug into the electronics enclosure vent penetrator.

	

4. Pump the vacuum until the gauge reads 10 in. Hg [34 kPa] vacuum. If you cannot pull a vacuum, try the suggestions following step 6, below.

	

5. Let the BlueROV2 and pump sit for 15 minutes.

6. If the gauge reads above 9 in. Hg [31 kPa] after 15 minutes, your seals are acceptable.

	

If the gauge reads below 9 in. Hg [31 kPa] vacuum after 15 minutes, you should check the following:

1. Make sure that the M3 screws on the front and back end caps of the battery and electronics enclosure using the M2.5 hex driver. If you are able to tighten one or more, attempt the vacuum test again.

2. Make sure that the penetrators on the battery and electronics enclosure are fully tightened. Check by attempting to loosen by hand. If you are able to loosen one or more, tighten them then attempt the vacuum test again.

3. Make sure that all of the O-rings are installed in the penetrators. If any are missing, install then attempt the vacuum test again.

4. Check that the face seal O-rings and radial O-rings are installed in the battery and electronics enclosures and in good condition. If you find a damaged or missing O-ring, install and attempt the vacuum test again.

If you are still having trouble holding vacuum, please contact us at <a href="mailto:support@bluerobotics.com">support@bluerobotics.com</a>

To continue assembling the BlueROV2, remove the acrylic tube and dome from the electronics enclosure.

## Installing the Power Wires from the Penetrators

To install the wires from the penetrators you will need the following parts and tools:

- 1 x Large (~#2) Phillips head screw driver

1. Connect the battery power bullet connectors to bullet connectors on XT60 to bullet connector adapter. 

	

2. Connect the Lumen power wire (red) to the Power Terminal Block with the other red wires. Use the rear screw terminal that is second from the bottom. To help keep the cable routing neat, bring the cable through the ESC wires and take out most of the slack.
	
	

3. Connect the Lumen ground wire (black) to the Power Terminal Block with the other black wires. Use the rear screw terminal that is second from the bottom. To help keep the cable routing neat, bring the cable through the ESC wires and take out most of the slack.
	
	

## Installing the Signal Wires from the Penetrators
	
To install the wires from the penetrators you will need the following parts and tools:

- 1 x Small (~2 mm) flat head screw driver

1. Connect the Lumen signal wire to the Pixhawk channel 7 with the yellow wire oriented toward the bottom of the Pixhawk. 

	

2. Connect the Bar30 cable to the I<sup>2</sup>C port on the Pixhawk.

	

3. Connect the motor wires to the motor wire terminal block, as shown in the diagrams below.

	

		

4. Connect the female tether wire connector with BLUE and WHITE wires to the extension cable that is connected to the Fathom-X Tether Interface Board. The other 6 wires can do not need to be connected to anything the operate the ROV. They are for future expansion.

	

If you received your BlueROV2 prior to August 7th, 2018, the following step applies to R1 tethers:

Connect the tether wires to the Fathom-X Tether Interface Board. The other 6 wires can do not need to be connected to anything the operate the ROV. They are for future expansion.

   

If you received your BlueROV2 prior to March 14th, 2017 you will need to [install the SOS Leak sensor using the archived instructions.](/brov2/assembly-pre201703/#installing-the-sos-leak-sensor)

## Cable Routing

To route the cables in the Electronics Enclosure so that they will not snag on the Watertight Enclosure for ROV/AUV (4" Series) with Dome End Cap installed you will need the following parts and tools:

- 3 x 5 1/2" zip ties
- 1 x Wire strippers or scissors

1. On the starboard side (Pixhawk side) collect the Bar30 wires and the Lumen signal wire and zip tie them to the long hex standoff slightly forward of the Motor Terminal Block using one zip tie. Make sure that the locking head of the zip tie and the wires are oriented to the inside of the long hex standoff.

	

2. On the port side (Fathom-X Tether Interface Board side) collect the Fathom Tether wires and zip tie them to the long hex standoff approximately even with the back of the Fathom-X Tether Interface Board and approximately even with the Motor Terminal Block. Make sure that the locking heads of the zip ties and the wires are oriented to the inside of the long hex standoff. 

	

# Final Assembly

## Adding Desiccant to the Electronics Enclosure

If you ordered your BlueROV2 prior to February 14, 2018 you will need to order [Moisture Indicating Silica Gel Desiccant](https://bluerobotics.com/store/tools/desiccant-r1/) in order to complete this step. This step is optional, but it will improve the usability of the BlueROV2, especially if you are planning on operating your ROV in humid environments with cold water.

The desiccant will absorb humidity that is inside of the Electronics Enclosure to prevent the dome from fogging up during dives. It will turn pink as it absorbs humidity.

1. Fill one of the Desiccant Bags with Moisture Indicating Silica Gel Desiccant and close the draw string. Make sure that you close the lid of the Moisture indicating Silica Gel Desiccant after you have filled the bag. It will become saturated in about a day if left open to air. 



2. Install the desiccant bag near the Fathom-X Tether Interface. This step will have to be combined with installing the Watertight Enclosure (4" Series) over the Electronics Tray since the bag will be "floating" inside of the enclosure

[Pictures Coming Soon]

## Mounting the Electronics Enclosure onto the Frame

To mount the Electronics Enclosure to the frame you need the following parts and tools:

- 1 x Watertight Enclosure for ROV/AUV (4" Series) with Dome End Cap installed
- 1 x Bag with four M3x16 screws
- 1 x 2.5 mm hex driver

1. Apply silicone grease to the two radial O-rings on the O-Ring Flange (4" Series) that is attached to the Electronics Tray then install the Watertight Enclosure (4" Series) with installed Dome End Cap to the O-Ring Flange (4" Series). 

2. Mount the Electronics Enclosure to the frame using the M3x16 screws so that the dome is on the same side as the front center panels (the center panels _without_ the 3 large holes). Install the M3x16 screws through the clips and into the Enclosure Cradle (4" Series). It is easier to install these screws if the clips are not fully tightened until all screws are through the clips and threading into the Enclosure Cradle (4" Series). This allows to clips to rotate so you can find the threaded hole in the Enclosure Cradle (4" Series) easily. 

	

## Mounting the Thrusters to the Frame

If you ordered your BlueROV2 prior to September 13, 2017, see the [archived thruster mounting instructions here](/brov2/assembly-pre201703/#mounting-the-thrusters-to-the-frame). Once you have mounted the thrusters, please return to these instructions to continue with [mounting the lights](/brov2/assembly/#mounting-the-lights).

To mount the thrusters to the frame, you need the following parts and tools:

- 1 x 2.5 mm hex driver
- 3 x T200 Thruster with Clockwise Propeller installed
- 3 x T200 Thruster with Counter-Clockwise Propeller installed
- 1 x Bag with 16 M3x16 screws and 8 M3x12 screws in smaller bag
- 1 x Assembled ROV frame

Note: If you received your BlueROV prior to March 14th, 2017 you will need to install the Counter-Clockwise Propellers. See [the archived instructions](/brov2/assembly-pre201703/#changing-the-propellers) for details.

The horizontal thrusters have two mounting options. One is at a 45° angle to forward, and the other is at a 30° angle to forward. The thrusters mounted at 45° will give you equal thrust in all directions. Mounting the thrusters at 30° will give you 25% more forward thrust in exchange for 25% less thrust in strafing. To mount the thrusters at 45° use the holes shown in the picture below. The hole with the asterisk is the hole that should be closest to the nose cone on the thruster.



To mount the thrusters at 30° use the holes shown in the pictures below. The hole with the asterisk is the hole that should be closest to the nose cone on the thruster.



For the sake of clarity, the hole with the asterisk on the thruster shown below is the hole that is closest to the nose cone.



Here is a diagram of where the thrusters go, and how they should be oriented. The green thrusters should have counter-clockwise propellers and blue thrusters should have clockwise propellers. The order of installation matters here. You cannot get the front thrusters on if the rear ones were installed first.

<p align="center">

</p>

<i class="fa fa-exclamation-triangle fa-fw fa-2x text-warning"></i> DO NOT use threadlocker unless you have threadlocker rated for use with polycarbonate.

1. Install thrusters 1 and 2 underneath the front center panels, using the M3x16 screws. Tighten the screws so that they indent the frame slightly. It is physically possible to keep turning the screw at this point, but it isn't recommended. 

2. Install thrusters 5 and 6, using the M3x12 screws on the side panels. Tighten the screws so that they indent the frame slightly.

3. Install thrusters 3 and 4 underneath the rear center panels, using the M3x16 screws. Tighten the screws so that they indent the frame slightly.

## Mounting the Lights

To install the Lumen mounts you will need the following parts and tools:

- 1 x Bag with four M3x12 socket head cap screws 
- 1 x 2.5 mm hex driver 
- 1 x BlueROV2 frame
- 1 x Threadlocker

1. Apply one drop of threadlocker to each of the M3x12 screws. Roll the screws around on a paper towel to evenly spread the threadlocker and to remove excess threadlocker.

2. Install the Lumens in the locations specified depending on how many light pairs you have. Installing the lights outside the frame reduces the amount of backscatter the camera sees. Make sure not to overtighten the screw that goes into the slot. Only tighten it so that it slightly indents the frame. 

	

## Mounting the Tether to the Frame

The tether needs to be firmly mounted to the frame to prevent the tether penetrator from being loosened through normal use. To do this, you will need the following parts and tools:

- 1 x Bag with thimble and 5 large zip ties
- 1 x Fathom Tether 
- 1 BlueROV2 frame

1. Loop the tether around the plastic thimble at a point about 12 inches (30 cm) away from the tether penetrator.
	
2. Firmly attach 3 of the zip ties, alternating directions as they are installed, around the tether right where it enters and exits the thimble. Hold the tether firmly in place against the thimble until it is secured.

		
	
3. Attach the thimble to the rear panel as shown

		
	
## Thruster and Lumen Cable Management

To clean up the thruster and lumen wires, you will need the bag of 30 zip ties and your scissors/wire cutters. 

The primary goal of Thruster and Lumen cable management is to prevent the wires from getting cut by the propellers. Make sure to check that no wire can reach a propeller after you have finished routing the cables. Below are some examples of what the cable routing should look like.







## Installing the Fairings and Buoyancy

The buoyancy comes preinstalled in the fairings, but make sure it is still in all of the fairings prior to installing the fairings. To install the fairings, you will need the following parts and tools:

- 4 x Fairings with buoyancy installed 
- 1 x Bag with 16 self tapping screws 
- 1 x \#1 Phillips head screwdriver 

1. Install the screws through the center panels and into the fairings.
	
	
	
## Mounting Ballast to the Frame

To mount the ballast to the frame you need the following parts and tools:

- 7 x 200g ballast weights
- 7 x 8-16 Thread, 5/8" Long, Thread-Forming Screw   
- 1 x \#2 phillips head screwdriver

To get the longest battery life and the best driving experience, it is important to have the ROV close to balanced from front to back in water and close to neutrally buoyant. Trimming the ballast may involve a bit of trial and error. The pictures below should provide a good starting point for mounting ballast if you have a stock BlueROV2 with the [recommended battery.](http://www.hobbyking.com/hobbyking/store/uh_viewItem.asp?idProduct=56844)

<b> <font size="4"> BlueROV2 with 2 <i> Lumen </i> Lights </font> </b> 
<p align="center">

</p>

<b> <font size="4"> BlueROV2 with 4 <i> Lumen </i> Lights </font> </b> 
<p align="center">

</p>

# Topside Setup 

If you ordered your BlueROV2 on or after August 7th, 2018, your kit will include a _Fathom-X Tether Interface (FXTI)_. Please refer to the [_FXTI_ documentation](http://docs.bluerobotics.com/fxti/#usage) for connection instructions.



If you ordered your BlueROV2 prior to August 7th, 2018, you will need the following parts and tools:

- 1 x Fathom-X Tether Interface Board
- 1 x 2 mm flat head screw driver
- 1 x Computer (Mac, Windows, Linux)
- 1 x Ethernet cable 
- 1 x USB to Ethernet adapter (if your computer does not have an Ethernet Port)
- 1 x Mini-USB cable

1. Connect the Fathom Tether to the Fathom-X Tether Interface Board. 

2. Connect the Ethernet port of the Fathom-X Tether Interface Board to you computer. If you do not have an Ethernet port on you computer connect the Ethernet port on the Fathom-X Tether Interface Board to a USB to Ethernet adapter then connect the adapter to your computer.

3. Connect your Mini-USB the the Fathom-X Tether Interface Board and to a USB power supply that can supply at least 500 milliamps. Most computer USB ports can do this, but if the "Link" LED does not light up try using a USB charger.



# Next Steps

First, set up the software on your topside computer. Please see our [Software Setup](/brov2/software-setup/) page.

Next, refer to the [Operating Manual](/brov2/operation/) to learn how complete your first dive.

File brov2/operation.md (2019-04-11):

---
layout: default
title: BlueROV2 Operating Manual
permalink: /brov2/operation/
order: 1
topnavbar: brov2
nav:
- Introduction: operating-manual-intro
- - Safety: safety
- Batteries: batteries
- - LiPo Safety: lipo-safety
- - Charging: how-to-charge-your-battery
- - Swapping Batteries: swapping-batteries
- First Dive: getting-ready-for-your-first-dive
- - Connecting Batteries: connecting-your-batteries
- - Topside Setup: setting-up-your-topside-control
- - Vacuum Test: vacuum-test
- - Controller Functions: controller-functions
- - Dive Modes: dive-modes
- Pre-Dive Checklists: pre-dive-checklists
- - Comprehensive Checklist: comprehensive-checklist
- - Pre-Dive Checklist: pre-dive-checklist
- Launch: launch
- - All Launches: all-launches
- - Boat Launch: boat-launch
- - Shore Launch: shore-launch
- - Dock Launch: dock-launch 
- Operation: operation
- - Tether Managament: tether-management
- - Driving Guidelines: driving-guidelines
- - Between Dives: storage-between-dives
- Recovery: recovery
- - Powered Recovery: powered-recovery
- - Unpowered Recovery: unpowered-recovery
- Post-Mission Checklist: post-mission-checklist
- Troubleshooting: troubleshooting
- Preventative Maintenance: preventative-maintenance
- - Every 100 Hours: every-100-hours-of-operation-or-every-6-months 
- Connection Diagrams: connection-diagrams
- Updating Software: updating-software
- - QGroundControl: qgroundcontrol
- - Companion: companion
- - ArduSub: ardusub
- Advanced Information: advanced-information
- Issue Reporting: issue-reporting

store-links:
- BlueROV: https://www.bluerobotics.com/store/rov/bluerov2/

manual-links:
- Specifications: /brov2/
- Assembly Manual: /brov2/assembly/
- Software Setup: /brov2/software-setup/

redirect: https://bluerobotics.com/learn/bluerov2-operation/
---



# Operating Manual Intro

The information on this page is for operating the BlueROV2. In order to operate the BlueROV2, it must be assembled and the software must be set up. If you have not assembled your BlueROV2, please see our [Assembly Manual](/brov2/assembly/). If you have not completed the software setup, please see our [Software Setup](/brov2/software-setup/) page.

## Safety 

<i class="fa fa-exclamation-triangle fa-fw fa-2x text-warning"></i> When working with electricity, especially in water, always practice caution. Always ensure that connections are secure and watertight. Keep your body away from spinning motors and propellers.

# Batteries

We recommend using LiPo batteries for the _BlueROV2_. If you do not have any experience with LiPo batteries, [our Battery Selection Guide](/battery/) has good introductory information on LiPo batteries. 

## LiPo Safety

[Our Battery Selection Guide](/battery/#lipo-safety) has several links to detailed LiPo safety information. The highlights are as follows:

- Charge LiPo batteries in a fire proof bag
- Let LiPo batteries cool off for at least 15 minutes after use before charging
- Never leave a LiPo battery unattended when charging
- Install a smoke detector in the area where you charge your LiPo batteries

## How to Charge Your Battery

To ensure that your LiPo batteries last as long as possible, it is important to not discharge the battery below 3.2 volts per cell or 12.8 volts if you are using a 4S battery.  

A nominal 14.8 volt (a 4s pack) LiPo battery is fully charged when it reaches 16.8 volts (4.2 volts per cell). If you charge a 4S battery beyond 16.8 volts, the battery may become damaged or catch fire. To safely charge a LiPo battery, you should charge with a LiPo-compatible charger. A LiPo-compatible charger will prevent over-charging; it will also balance the cells. A good rule of thumb is to charge your LiPo battery at less than or equal to "1C" or 1 time its capacity. So, if you are using the 10,000mAh battery, you would want to charge at or less than 10 amps.

## Swapping Batteries

To exchange batteries in the _BlueROV2_ use the following procedure:

1. Move the _BlueROV2_ to a dry area.
2. Remove the vent plug from the vent penetrator. Place the vent plug in a safe place
3. Remove the 4-hole end cap from the battery enclosure
4. Disconnect battery and remove it from the battery enclosure.
5. Connect new battery and place it in the battery enclosure.
6. Install 4-hole end cap onto battery enclosure.
7. Check the O-rings on the vent plug, then install it into the vent penetrator.

# Getting Ready for Your First Dive

Before putting the BlueROV2 in the water, there are a few things that you need to do. 

Your first dive should be in a body of water that is shallow, still, and clear. We recommend a pool or a test tank. Testing in a more controlled environment will provide a good opportunity to check that the ROV is ballasted correctly. It will also allow you to confirm that your controller is set up correctly and your ROV is behaving how you expect it to. 

## Connecting Your Batteries

To get ready for your first dive, you need to start by connecting a charged battery using the same process as shown in the [Swapping Batteries](#swapping-batteries) section. 

## Setting up Your Topside Control

To set up your topside control follow the instructions on the [Software Setup](/brov2/software-setup/) page.

## Vacuum Test 

To perform a vacuum test on the _BlueROV2_, you need the vacuum pump that came with your kit. It is important to do a vacuum test prior to putting the _BlueROV2_ in the water for the first time. It is also important to perform a vacuum test after changing anything that could compromise a seal, such as changing out a penetrator or an O-ring.

The vacuum test can be performed using the following procedure:

1. Remove the vent plugs from both the electronics and the battery enclosure.
2. Install one of the vacuum plugs on the included tee in the electronics enclosure and the other in the battery enclosure.
3. Pump until the gauge reads 10 in. Hg [34 kPa] vacuum.
4. Let the _BlueROV2_ and pump sit for 15 minutes.
5. If the gauge reads above 9 in. Hg [31 kPa] vacuum after 15 minutes, your seals are acceptable.

If the gauge reads below 9 in. Hg [31 kPa] vacuum after 15 minutes, you should check the following:

1. Make sure that the M3 screws on the front and back end caps of the battery and electronics encloure using the M2.5 hex driver. If you are able to tighten one or more, attempt the vacuum test again. 
2. Make sure the the penetrators on the battery and electronics enclosure are fully tightened. Check by attempting to loosen by hand. If you are able to tighten one or more, attempt the vacuum test again.
3. Make sure that all of the O-rings are installed in the penetrators. If any are missing, install then attempt the vacuum test again.
4. Check that the Face seal O-rings and radial O-rings are installed in the battery and electronics enclosures and in good condition. If you find a damaged or missing O-ring, install and attempt the vacuum test again.

## Controller Functions

The BlueROV2 comes with the button setup shown below as a default:



If you do not like the button settings, you can change the button setup in QGroundControl.

1. Go to _Settings_ then select "Joystick" 

2. Under "Button actions:" QGroundControl shows what all buttons are currently set to control.

3. Press the button that you are interested in changing. The button number will light up.

4. Select what you would like the button to do from the dropdown to the right of the button number.

## Dive Modes

- In **Manual Mode** the BlueROV2 will only output motor controls based on the pilot input from the joysticks. There is no feedback stabilization, heading holding, or depth holding.

- In **Stabilize Mode** the BlueROV2 will stabilize roll to level and it will maintain heading when not commanded to turn. The vertical control is left entirely to the pilot.

- In **Depth Hold Mode** the BlueROV2 will hold depth unless you command it to dive/ascend. It will also stabilize roll to level and maintain heading when not commanded to turn.

# Pre-Dive Checklists

## Comprehensive Checklist

This checklist is more thorough than the [Pre-Dive Checklist](#pre-dive-checklist) and should be done in a couple of circumstances:

- After travel by airplane
- After extended travel by car or boat (>1 hour)
- After taking off the electronics enclosure
- After replacing or exchanging penetrators
- After replacing any sealing O-ring

**Comprehensive Checklist**

- Check that the ROV has connected to QGroundControl
- Tighten the M5x16 screws that hold the frame to the center and bottom panels using the short part of the M3 hex key as the handle or an M3 hex driver.
- Tighten the M3x12 screws that hold the back end caps to the flange seals using the M2.5 hex driver.
- Tighten the M3x16 screws that hold the clips to the electronics enclosure.
- Tighten the M3x12 screws that hold the dome and the front battery end cap to the flange seals using the M2.5 hex driver.
- Gently attempt to twist the ballast weights clockwise.
- Pull on the side panels and attempt to twist the frame. 
- Pull on the cable bundles going into the 14 hole end cap.
- Pull on and twist the tether thimble.
- Attempt to loosen all of the penetrators by hand.
- Check that the vent plugs are installed.
- Push and twist the battery enclosure.
- Visually check that all screws holding the back end caps are installed and look tight.
- Pull on all of the thrusters.
- Grab and shake the fairings.
- Pull on the _Lumens_.
- Visually check that all screws holding the dome and front battery end cap are installed and look tight.
- Visually check the radial seals on the electronics and battery enclosure.
- Put the ROV on the ground and make sure that people are clear of the thrusters.
- Check to make sure the camera tilt function and lights work. If they do not, please see the [Troubleshooting](#troubleshooting) section.
- Put the ROV in manual mode.
- Arm the ROV.
- Press the forward/reverse stick forward to check that the vectored thrusters are spinning freely.
- Press the ascend/descend stick forward to check that the vertical thrusters are spinning freely.
- Disarm the ROV.
- Launch.

## Pre-Dive Checklist

This checklist should be done every time the ROV is put into the water, prior to putting the ROV in the water. This checklist starts after you have connected the battery, reinstalled the battery enclosure end cap, and reinstalled the battery enclosure vent plug.

- Check that the ROV has connected to QGroundControl.
- Gently attempt to twist the ballast weights clockwise.
- Pull on the side panels and attempt to twist the frame. 
- Pull on the cable bundles going into the 14 hole end cap.
- Pull on and twist the tether thimble.
- Attempt to loosen all of the penetrators by hand.
- Check that the vent plugs are installed.
- Push and twist the battery enclosure.
- Visually check that all screws holding the back end caps are installed and look tight.
- Pull on all of the thrusters.
- Grab and shake the fairings.
- Pull on the _Lumens_.
- Visually check that all screws holding the dome and front battery end cap are installed and look tight.
- Visually check the radial seals on the electronics and battery enclosure.
- Put the ROV on the ground and make sure that people are clear of the thrusters.
- Check to make sure the camera tilt function and lights work. If they do not, please see the [Troubleshooting](#troubleshooting) section.
- Put the ROV in manual mode.
- Arm the ROV.
- Press the forward/reverse stick forward to check that the vectored thrusters are spinning freely. Do not run the thrusters for more than 30 seconds in air.
- Press the ascend/descend stick forward to check that the vertical thrusters are spinning freely. Do not run the thrusters for more than 30 seconds in air.
- Disarm the ROV
- Now you are ready to launch

# Launch



The _BlueROV2_ can be launched in many conditions. Some conditions require special care.

## All Launches

- Do not launch the ROV near swimmers or divers.  
- Do not release the ROV prior to it touching the water. If necessary, use the tether to lower it down. When lowereing the ROV, keep the dome away from any hard or sharp objects.
- Do not launch in water that is too shallow to freely drive the ROV.
- Keep the ROV away from boats that do not know that the ROV is in the water.
- Do not arm until the ROV is in the water and the launcher is clear of the ROV.

## Boat Launch

- Keep the ROV and tether clear of the boat's propellers or jets.
- Make sure that the captain of the boat knows that the ROV is about to be launched.

## Shore Launch

- Do not launch the ROV in heavy surf.
- You may need to walk the ROV into the water to get to a point where the water is deep enough to drive the ROV.

## Dock Launch

# Operation

## Tether Management

When diving the _BlueROV2_ the tether will require some active management. Here are some guidelines for good tether management:

- Keep the tether away from propellers or jets if you are operating on a boat.
- Keep the tether and ROV away from other boats that are not aware that it is in the water.
- Keep the tether away from sharp objects such as coral, rocks, etc.
- Do not deploy too much tether. Excess tether in the water will add drag to the ROV and opportunity for the tether to get caught on something.
- Do not deploy the tether over sharp edges or rough ground.
- Do not step on the tether.

## Driving Guidelines

- Do not drive into a sandy bottom. If you do drive into a sandy bottom, stop driving the vehicle and allow it to float up to prevent sand from getting into the vertical thrusters.
- Drive smoothly and on low gain when possible to maximize battery life.
- Do not touch coral with the ROV to prevent damage to the coral.
- Avoid driving into seaweed when possible. Seaweed can get sucked into and stop the thrusters from spinning.
- When diving, it is helpful to follow down a chain or a line to give a frame of reference. 

## Storage Between Dives

If you have a break between dives where the _BlueROV2_ is out of the water for more than 15 minutes, make sure to keep it in a shaded area. If there is no shade nearby, a towel draped over the ROV will supply sufficient shade. 

# Recovery

<i class="fa fa-exclamation-triangle fa-fw fa-2x text-warning"></i> Disarm the _BlueROV2_ prior to attempting to recover it.

## Powered Recovery

Typically, you will be recovering the _BlueROV2_ when it is under power.

- The ROV pilot should find the tether and follow it back to the launching area.
- While the pilot is driving back pull in the tether slack. Clean debris off of the tether and inspect for cuts or nicks while pulling in.
- When the ROV arrives back to the launching location, disarm the ROV.
- Pick up the ROV directly if practical, or pull the ROV up using the tether. Avoid sharp or hard object while lifting the ROV by the tether; allow space for the ROV to swing.
- Remove the vent plug from the battery enclosure vent penetrator.
- Disconnect the battery.

## Unpowered Recovery

If the ROV loses power or connection to QGroundControl while diving, you should do the following:

- Pull the tether in at a moderate pace. Don't try to pull it in as fast as possible.

# Post Mission Checklist

- Rinse down with fresh water
- If you were operating in a sandy environment or seaweed, clean sand and seaweed from the thrusters.

# Troubleshooting

## Re-Load BlueROV2 Default Parameters

- If your camera tilt or lights do not work when the appropriate buttons are pushed, please re-load the BlueROV2 default parameters.
- Navigate to the _Frame_ tab of the _Vehicle Setup_ page and select _Load Vehicle Default Parameters_ and then either _Blue Robotics Blue ROV2_ or _Blue Robotics BlueROV2 Heavy_ depending on your hardware configuration. 
- Wait for the green loading bar to finish writing the parameters.



# Preventative Maintenance

<i class="fa fa-exclamation-triangle fa-fw fa-2x text-warning"></i>
Only clean the dome and acrylic tubes with acrylic specific cleaner or plain water. Solvents, alcohol and other cleaners will craze and damage the material.

## Every 100 Hours of Operation or Every 6 Months 

- Replace _Lumen_ mount O-rings. 
- Replace radial battery cap O-rings on the side that you open and close when swapping batteries.
- Replace vent plug O-rings.

# Connection diagrams

These diagrams outline all of the electrical connections between components in the ROV. There is a different diagram for each version of the ROV that Blue Robotics has produced.

- [BlueROV2 with red-wire (BEC) ESCs](/brov2/cad/connections/BlueROV2_bec.pdf) (Pre-2018)
- [BlueROV2 with no-red-wire ESCs](/brov2/cad/connections/BlueROV2_no_bec.pdf) (2018 and later)
- [BlueROV2 Heavy](/brov2/cad/connections/BlueROV2_heavy.pdf)

# Updating Software

## QGroundControl

QGroundControl software release notes are [here](https://raw.githubusercontent.com/bluerobotics/qgroundcontrol/3.2.4/BlueRobotics-Revision-Notes.txt). To update QGroundControl, simply download and install the latest stable version of QGC (BlueRobotics flavor) from one of the links below:

[Windows](https://s3.amazonaws.com/downloads.bluerobotics.com/QGC/QGroundControl-installer.exe)

[Mac](https://s3.amazonaws.com/downloads.bluerobotics.com/QGC/QGroundControl.dmg)

[Linux](https://s3.amazonaws.com/downloads.bluerobotics.com/QGC/QGroundControl.AppImage)

## Companion

Companion software release notes are [here](https://raw.githubusercontent.com/bluerobotics/companion/master/release-notes.txt). To perform a companion update update:

- Plug a _fully charged_ battery into the ROV and connect the tether to your computer.
- Navigate to [192.168.2.2:2770/network](http://192.168.2.2:2770/network) in your browser and ensure that the ROV has access to a WiFi network. If you do not see a webpage at this address, you need to perform the update according to the instructions [here](http://discuss.bluerobotics.com/t/software-updates/1128).
- Navigate to [192.168.2.2:2770/system](http://192.168.2.2:2770/system). Click the button that says 'Update companion'. If you do not see this button, then the companion software is up to date.
- The update process will take between 5 and 20 minutes depending on the Internet connection speed. Wait for the update process to complete.
- When it completes, refresh your browser. The companion version should be updated, and the update available message should no longer appear.
- If the update fails (usually due to a loss of internet connectivity), you will be warned that the ROV will reboot and to leave the battery plugged in. At this point, once you are able to refresh the webpage, it is safe to either power down the ROV or attempt the update again.

## ArduSub

ArduSub software release notes are [here](https://raw.githubusercontent.com/ArduPilot/ardupilot/master/ArduSub/ReleaseNotes.txt). The autopilot installed on a vehicle can be updated via the companion computer web interface:

- Power on your ROV and connect it to your computer
- Navigate to [192.168.2.2:2770/network](http://192.168.2.2:2770/network) and ensure that the ROV has an internet connection
- Navigate to [192.168.2.2:2770/system](http://192.168.2.2:2770/system). Click the button under the 'Pixhawk Firmware Update' section that says 'Stable'.
- Wait for the update process to complete, and you are finished!

# Advanced Information

The BlueROV2 is not designed to do just one thing, it is designed to be very flexible and adaptable to suit many applications. As such, there are flexible and advanced configuration options that are directly accessible to the end user. To learn more about the software and hardware that drives the BlueROV2, please visit [ardusub.com](https://www.ardusub.com/). There are also available a wide range of developer resources, and a strong marine hacking community at [discuss.bluerobotics.com](https://discuss.bluerobotics.com).

# Issue Reporting

We're always trying to make our documentation, instructions, software, and user experience better. If you're having an issue with anything, please report it so that we can address it as soon as possible! Here's where to do that depending on what's wrong:

- **ArduSub Issues:** For anything related to the ArduSub software that runs on the Pixhawk and controls the ROV, reports issues on the [ArduSub Github Issues Page](https://github.com/bluerobotics/ardusub/issues). If you're unsure where your issue should be posted, you can report it here.
- **QGroundControl Issues:** For anything related to the QGroundControl software, joystick setup, video streaming, etc., please report an issue on the [QGroundControl Github Issues Page](https://github.com/mavlink/qgroundcontrol/issues).
- **Documentation:** For anything related to the documentation and instructions here, please report an issue on the [Blue Robotics Documentation Github Issues Page](https://github.com/bluerobotics/bluerobotics.github.io/issues).

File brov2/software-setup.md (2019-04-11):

---
layout: default
title: BlueROV2 Software Setup
permalink: /brov2/software-setup/
order: 1
topnavbar: brov2
nav:
- Introduction: software-introduction
- Install QGroundControl: install-qgroundcontrol
- Network Setup: network-setup
- Joystick Setup: joystick-setup
- Update Software: update-software
- Joystick Calibration: joystickgamepad-calibration
- Button Setup: button-setup
- Sensor Calibration: sensor-calibration
- Configure Motor Directions: configure-motor-directions
- Voltage and Current Measurement Setup: voltage-and-current-measurement-setup
- SOS Leak Sensor Setup: sos-leak-sensor-setup
- To The First Dive!: to-the-first-dive
- Issue Reporting: issue-reporting

store-links:
- BlueROV: https://www.bluerobotics.com/store/rov/bluerov2/

manual-links:
- BlueROV2 Specifications: /brov2/
- Assembly Manual: /brov2/assembly/
- Operations Manual: /brov2/operation/

redirect: https://bluerobotics.com/learn/bluerov2-software-setup/
---

<script>
	var blacklistElements = []
	var osSpecificElements = []
	var osSpecific = ['install-qgroundcontrol',
		'network-setup',
		'joystick-setup']
		
$(document).ready(function(){
	// initialize collapse state
	$('#windowsDiv').collapse({toggle: false});
	$('#macDiv').collapse({toggle: false});
	$('#linuxDiv').collapse({toggle: false});
	
	// We don't show these sidebar-nav items until the user selects an OS
	var blacklist = ['Install QGroundControl',
	'Network Setup',
	'Update Software',
	'Joystick Setup',
	'Joystick Calibration',
	'Button Setup',
	'Sensor Calibration',
	'Configure Motor Directions',
	'Voltage and Current Measurement Setup',
	'SOS Leak Sensor Setup',
	'To The First Dive!']
	
	var sidebar = document.getElementById('sidebar');
	var children = sidebar.getElementsByTagName("a");

	for (var i = 0; i < children.length; i++) {
		var child = children[i];
		blacklist.forEach(function(item) {
			if (child.innerHTML == item) {
				blacklistElements.push(child);
			}
		});
		
		osSpecific.forEach(function(item) {
			if (child.href.split('#')[1] == item) {
				console.log('match', child);
				// Careful!, indices not guaranteed for modification step later on
				osSpecificElements.push(child);
			}
		});
	}
	
	// Hide these guys
	for (var i = 0; i < blacklistElements.length; i++) {
		var element = blacklistElements[i];
		element.style.display = "none";
	}	
});

function showBlacklistElements(os) {
	
	// Edit sidebar-nav links for headings repeated in each OS section
	for (var i = 0; i < osSpecificElements.length; i++) {
		var element = osSpecificElements[i];
		
		// Careful!, indices might not actually line up correctly
		element.href = "#" + osSpecific[i] + os;
	}
	
	// Show navigation options after OS selection
	for (var i = 0; i < blacklistElements.length; i++) {
		var element = blacklistElements[i];
		
		element.style.display = "block";
	}
}

function showWindows() {
	$('#windowsDiv').collapse('show'); 
	$('#macDiv').collapse('hide'); 
	$('#linuxDiv').collapse('hide'); 
	$('#commonDiv').collapse('show'); 
	showBlacklistElements('');
}
function showMac() {
	$('#macDiv').collapse('show'); 
	$('#linuxDiv').collapse('hide'); 
	$('#windowsDiv').collapse('hide'); 
	$('#commonDiv').collapse('show'); 
	showBlacklistElements('-1');
}
function showLinux() {
	$('#linuxDiv').collapse('show'); 
	$('#macDiv').collapse('hide'); 
	$('#windowsDiv').collapse('hide'); 
	$('#commonDiv').collapse('show'); 
	showBlacklistElements('-2');
}

$( document ).ready(function() {
    showWindows();
});
</script>



# Software Introduction

These are instructions for the first time that you set up your computer to work with the BlueROV2. If you have not assembled your BlueROV2, please see our [Assembly Manual](/brov2/assembly/) and assemble your BlueROV2 prior to setting up the software.

Select your operating system below to begin the installation and network configuration:

<a class="btn btn-default" href="#software-introduction" onclick="showWindows()">Windows</a>
<a class="btn btn-default" href="#software-introduction" onclick="showMac()">Mac</a>
<a class="btn btn-default" href="#software-introduction" onclick="showLinux()">Linux</a>

<div id="windowsDiv" class="collapse" markdown="1">

# Install QGroundControl

To connect your computer to the BlueROV2, you need to download and install QGroundControl:

- [Windows](https://s3.amazonaws.com/downloads.bluerobotics.com/QGC/QGroundControl-installer.exe)

# Network Setup

If your computer does not have an Ethernet port, you will need a USB to Ethernet adaptor. We recommend using [this one.](https://www.amazon.com/Cable-Matters-Ethernet-Network-Adapter/dp/B00ET4KHJ2)

**Network Settings**

1. Go to _Control Panel_ > _Network and Sharing Center_ and then choose "Change adapter settings".

	

2. Right click on the Ethernet adapter, then choose _Properties_.

	

3. In the properties dialog, choose _Internet Protocol Version 4 (TCP/IPv4)_, then click _Properties_.

	

4. Select "Use the following IP address" And enter 192.168.2.1 for the IP address and 255.255.255.0 for the Subnet mask. Then select OK.

	

**Firewall**

1. Go to _Control Panel_ > _Windows Firewall_ and then select "Allow an app or feature through Windows Firewall".

2. Select "Change Settings" and then select "Open source ground control app provided by QGroundControl dev team" or "QGroundControl".

	

# Joystick Setup

**Initial Setup for XBox Controllers on Windows**

For using the shift button functionality of XBox Controllers on Windows:

1. Go to Start -> Settings
2. Open the Gaming settings

	

3. Go to Game Bar tab from the left navigation panel
4. Uncheck the 'Open Game bar using this button on a controller' option

	

This will enable the XBox home button on the controller to be used as the Shift button for ROV controls.

**XBox 360 Controller** 

- Plug and Play

**XBox One Controller** 

- Wired: Plug and Play 
- Wireless: 
	1. Plug in [Microsoft XBox Wireless Adapter for Windows](https://www.amazon.com/Microsoft-Xbox-Wireless-Adapter-Windows-one/dp/B00ZB7W4QU).
	2. Turn on the controller, then press the Wireless Enrollment button on the top of the controller and on the wireless adapter.

**Logitech GamePad (F710 and F310)**

Logitech controllers should have the switch on the back set to "X".
</div>

<div id="macDiv" class="collapse" markdown="1">

# Install QGroundControl

To connect your computer to the BlueROV2, you need to download and install QGroundControl:

- [Mac](https://s3.amazonaws.com/downloads.bluerobotics.com/QGC/QGroundControl.dmg)

# Network Setup

If your computer does not have an Ethernet port, you will need a USB to Ethernet adaptor. We recommend using [this one.](https://www.amazon.com/Cable-Matters-Ethernet-Network-Adapter/dp/B00ET4KHJ2)

**Network Settings**

1. Go to _System Preferences_ > _Network_

2. If your computer has an Ethernet port, select Ethernet from the options on the left side. If you had to get a USB to Ethernet adapter, plug it in now then select it.

3. Select the dropdown next to "Configure IPv4" and then select "Manually"

4. Enter 192.168.2.1 for the IP Address and 255.255.255.0 for the Subnet Mask and then select apply.

	

# Joystick Setup

**XBox 360 Controller**

1. Download the driver [here](https://github.com/360Controller/360Controller/releases/download/v0.16.5/360ControllerInstall_0.16.5.dmg). For more information on this driver, see the [Readme.](https://github.com/360Controller/360Controller#about)
2. Install the XBox 360 controller driver.
2. Plug in the Windows XBox 360 Wireless Receiver for Windows.
3. Turn on the XBox 360 Controller.

**XBox One Controller**
There is currently no support for wireless use.

1. Download the driver [here](https://github.com/360Controller/360Controller/releases/download/v0.16.5/360ControllerInstall_0.16.5.dmg). For more information on this driver, see the [Readme.](https://github.com/360Controller/360Controller#about)
2. Install the XBox 360 controller driver.
2. Plug in the XBox One Controller directly to the computer using a micro USB cable.
3. Turn on the XBox One Controller.

**Logitech GamePad (F710 and F310)**

Logitech controllers should have the switch on the back set to "X"
</div>

<div id="linuxDiv" class="collapse" markdown="1">

# Install QGroundControl

To connect your computer to the BlueROV2, you need to download and install QGroundControl:

- [Linux](https://s3.amazonaws.com/downloads.bluerobotics.com/QGC/QGroundControl.AppImage)

# Network Setup

If your computer does not have an Ethernet port, you will need a USB to Ethernet adaptor. We recommend using [this one.](https://www.amazon.com/Cable-Matters-Ethernet-Network-Adapter/dp/B00ET4KHJ2)

**Network Settings**

1. Click the Network Icon in the toolbar at the top of the screen, and click "Edit Connections..."

	

2. Click "Add"

	

3. Select "Ethernet" for the connection type and click "Create..."

	

4. From the "Device MAC Address" dropdown, select the ethernet interface you want to use. If you are using the built in ethernet card on your computer, there will be only one choice. If you are using a USB to Ethernet adapter, find out which interface corresponds to the adapter by looking at the options before and after plugging the adapter into the computer.

	

5. Click the "IPv4 Settings" tab, and from the "Method" dropdown menu, select "Manual". Click "Add", and enter 192.168.2.1 for the Address, 255.255.255.0 for the Netmask and 0.0.0.0 for the Gateway. Click "Save..." to complete the setup.

	

# Joystick Setup

All required drivers for wired Xbox 360 controllers and Logitech F310 controllers come pre-loaded on Ubuntu 14.04 and 16.04, no setup necessary!

**Logitech GamePad (F710 and F310)**

Logitech controllers should have the switch on the back set to "X"
</div>
<div id="commonDiv" class="collapse" markdown="1">

# Update Software

There are two computers installed on the BlueROV2: a Pixhawk autopilot, and a Raspberry Pi 'companion' computer. Before proceeding, we will check that the software on both computers is up to date, and update the software if necessary.

## Companion

Companion is the software that runs on the Raspberry Pi. To perform a companion software update:

- Plug a _fully charged_ battery into the ROV and connect the tether to your computer.
- Navigate to [192.168.2.2:2770/network](http://192.168.2.2:2770/network) in your browser and ensure that the ROV has access to a WiFi network. If you do not see a webpage at this address, you need to perform the update according to the instructions [here](http://discuss.bluerobotics.com/t/software-updates/1128).
- Navigate to [192.168.2.2:2770/system](http://192.168.2.2:2770/system). Click the button that says 'Update companion'. If you do not see this button, then the companion software is up to date.
- The update process will take between 5 and 20 minutes depending on the Internet connection speed. Wait for the update process to complete.
- When it completes, refresh your browser. The companion version should be updated, and the update available message should no longer appear.
- If the update fails (usually due to a loss of internet connectivity), you will be warned that the ROV will reboot and to leave the battery plugged in. At this point, once you are able to refresh the webpage, it is safe to either power down the ROV or attempt the update again.

## ArduSub

ArduSub is the software that runs on the Pixhawk autopilot. To perform an ArduSub software update:

- Navigate to [192.168.2.2:2770/network](http://192.168.2.2:2770/network) and ensure that the ROV has an internet connection
- Navigate to [192.168.2.2:2770/system](http://192.168.2.2:2770/system). Click the button under the 'Pixhawk Firmware Update' section that says 'Stable'.
- Wait for the update process to complete, and you are finished!

# Joystick/Gamepad Calibration

Some joysticks require calibration before you can enable them for use with QGroundControl. If your joystick requires calibration, the *Joystick* tab on the *Vehicle Settings* page will be red, and you should follow these steps to calibrate your joystick. If your joystick does not require calibration, the *Joystick* tab will not be red, and you can skip this step!

1. Go to the *Vehicle Settings* page in QGroundControl, then click on the red *Joystick* tab in the sidebar on the left.

2. Ensure the 'TX Mode' selection is set to 3.

3. Click "Calibrate", then click "Next".
 
4. Follow the step-by-step instructions, move the sticks as indicated in the diagram in QGroundControl.

When completed, the *Joystick* tab will no longer be red, and the *Enabled* checkbox on the Joystick page should be checked.

# Button Setup

The default button setup for the BlueROV2 is as shown in the image below:



The button functions may be reconfigured in the *Joystick* tab on the *Vehicle Settings* page.

# Sensor Calibration

1. Go to the *Vehicle Settings* page in QGroundControl and select the red _Sensors_ tab in the sidebar on the left.
2. Choose `Roll90` for the *Autopilot Orientation* selection.
3. Click on the _Accelerometers_ and follow the instructions.
4. Click on _Compass_ and follow the instructions.

When completed, the _Sensors_ tab will no longer be red.

# Configure Motor Directions

The motor directions for the BlueROV2 must be configured prior to operation.

<i class="fa fa-exclamation-triangle fa-fw fa-2x text-warning"></i>Be sure to keep all body parts and clothing clear of thrusters while the BlueROV2 is armed.

<i class="fa fa-exclamation-triangle fa-fw fa-2x text-warning"></i>**Do not** run thrusters for longer than 30 seconds in air.

1. Go to the *Vehicle Settings* page in QGroundControl and select the _Motors_ tab in the sidebar on the left.
1. Read and understand the instructions on the setup page
1. Arm the BlueROV2 by clicking the switch on the page
1. One at a time, move each slider, and make sure that the motor that spins is pushing air in the correct direction. If a motor is spinning in the wrong direction, click the corresponding checkbox under the 'Reverse Motor Direction' section to correct the motor rotation.
1. When you are finished with the setup, disarm the ROV by clicking the switch

    

# Voltage and Current Measurement Setup 

The default settings for voltage and current measurement are for the [Multistar High Capacity 4s 10,000mAh](http://www.hobbyking.com/hobbyking/store/uh_viewItem.asp?idProduct=56844) battery that we recommend. If you select a different battery, you can adjust your voltage and current measurement setup by going to _Settings_ then select _Power_. The only thing that you will need to change is the "Battery capacity", which can changed by simply typing in the size of the battery into the box.



# SOS Leak Sensor Setup

In the Safety tab, select "Pixhawk Aux6" as the leak detector pin, and set the Logic when dry to "Low."



# To The First Dive! 

Your computer setup is now complete! Please see our [Operations Manual](/brov2/operation/) to finish getting ready for your first dive!

</div>

# Issue Reporting

We're always trying to make our documentation, instructions, software, and user experience better. If you're having an issue with anything, please report it so that we can address it as soon as possible! Here's where to do that depending on what's wrong:

- **ArduSub Issues:** For anything related to the ArduSub software that runs on the Pixhawk and controls the ROV, reports issues on the [ArduSub Github Issues Page](https://github.com/bluerobotics/ardusub/issues). If you're unsure where your issue should be posted, you can report it here.
- **QGroundControl Issues:** For anything related to the QGroundControl software, joystick setup, video streaming, etc., please report an issue on the [QGroundControl Github Issues Page](https://github.com/mavlink/qgroundcontrol/issues).
- **Documentation:** For anything related to the documentation and instructions here, please report an issue on the [Blue Robotics Documentation Github Issues Page](https://github.com/bluerobotics/bluerobotics.github.io/issues).

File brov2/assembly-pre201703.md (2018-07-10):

---
layout: default
title: BlueROV2 Kit Assembly (Pre March 2017)
permalink: /brov2/assembly-pre201703/
order: 1
topnavbar: brov2
nav:
- Introduction: assembly-intro
- - Safety: safety
- Required Tools: required-tools-not-included
- What's Included: whats-included
- - Frame: frame
- - Electronics Enclosure: electronics-enclosure
- - Battery Enclosure: battery-enclosure
- - Thrusters: thrusters
- - Fairings: fairings
- - Tether: tether
- - Tools: tools
- Optional Configurations: optional-configurations
- - Standard Electronics: standard-electronics-package
- - Advanced Electronics: advanced-electronics-package
- - Lights: lights
- What's Not Included: what-you-need-for-operation-that-is-not-included
- Frame Assembly: assembling-the-frame
- - Battery Enclosure: mounting-the-battery-enclosure-to-the-bottom-panel
- - Center Panels: assembling-the-center-panels
- - Frame: assembling-the-frame-1
- Electronics Tray Assembly: assembling-the-electronics-tray
- - Advanced Overview: advanced-overview
- - Electronics Enclosure: partially-disassembling-the-electronics-enclosure
- - Connecting ESCs: connecting-the-esc-power-and-motor-wires
- - Standard Electronics: installing-the-standard-electronics
- - Advanced Electronics: installing-the-advanced-electronics
- Electronics Tray Wiring: wiring-the-electronics
- - Power Module: connecting-the-pixhawk-power-module
- - Standard Electronics Wiring: wiring-the-standard-electronics
- - Advanced Electronics Wiring: wiring-the-advanced-electronics
- - Signal Wiring: signal-cable-wiring
- Changing Propellers: changing-the-propellers
- Cable Installation: installing-the-cables
- - Penetrator Installation: installing-the-penetrators
- - End Cap Installation: installing-the-end-cap
- - Finishing Battery Enclosure: finishing-the-battery-enclosure
- - Optional Preliminary Vacuum Test: optional-preliminary-vacuum-test
- - Installing the SOS Leak Sensor: installing-the-sos-leak-sensor
- - Penetrator Power Wiring: installing-the-power-wires-from-the-penetrators
- - Penetrator Signal Wiring: installing-the-signal-wires-from-the-penetrators
- - Electronics Cable Routing: electronics-tray-cable-management
- Final Assembly: final-assembly
- - Mounting Electronics Enclosure: mounting-the-electronics-enclosure-onto-the-frame
- - Mounting Thrusters: mounting-the-thrusters-to-the-frame
- - Mounting Lights: mounting-the-lights
- - Mounting the Tether: mounting-the-tether-to-the-frame
- - External Cable Management: thruster-and-lumen-cable-management
- - Installing Fairings: installing-the-fairings-and-buoyancy
- - Ballast: mounting-ballast-to-the-frame
- Topside Setup: topside-setup
- Next Steps: next-steps
- Issue Reporting: issue-reporting

store-links:
- BlueROV: http://bluerobotics.com/store/rov/bluerov2/

manual-links:
- Software Setup: /brov2/software-setup/
- Specifications: /brov2/
- Operations Manual: /brov2/operation/

---



# Assembly Intro

**THIS PAGE IS THE ASSEMBLY INSTRUCTIONS FOR BLUEROV2 KITS SHIPPED PRIOR TO MARCH 2017.** Newer kits should refer to the [main assembly instructions here](/brov2/assembly/).

The _BlueROV_ kit comes almost ready to dive. The assembly can be completed with basic hand tools; no soldering or potting is required. We have included a couple of the tools that will be used most often to make assembly and regular use go as smoothly as possible.

## Safety 

<i class="fa fa-exclamation-triangle fa-fw fa-2x text-warning"></i> When working with electricity, especially in water, always practice caution. Always ensure that connections are secure and watertight. Keep your body away from spinning motors and propellers.

<i class="fa fa-exclamation-triangle fa-fw fa-2x text-warning"></i> When working with silicone grease and threadlocker, take care to minimize skin contact. Wear protective nitrile or PVC gloves when handling.

# Required Tools Not Included

- 2.5 or 3mm Flat Head Screwdriver
- \#2 Phillips Head Screwdriver
- Wire Cutters or Scissors (for cutting zip ties)
- Thread-locker such as [Loctite 243](https://www.amazon.com/Loctite-1330799-Resistant-thread-locker-6-milliliter/dp/B004L439FE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)
- Tweezers (for assistance installing wires into terminal blocks)
- Isopropyl Alcohol or isopropyl alcohol wipes
- Vacuum Pump such as [this one](https://www.amazon.com/HFS-Brake-Bleeder-Vacuum-Tuner/dp/B00NP60URE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)

# What's Included

## Frame

Quantity      | Part														| Usage
------------- | ------------------------------------------------------------| ----------------------
2             | Front Center Panel (1/2" thick black HDPE)        			|    
2             | Rear Center Panel (1/2" thick black HDPE)           		|     	       
1             | Bottom Panel (1/2" thick black HDPE)                       	|  
2             | Side Panel (3/8" thick black HDPE)                       	|
2             | Electronics Enclosure Cradle (Black Anodized Aluminum)  	| Mounting the electronics enclosure to the frame
8 			  | M4x18 Socket Head Cap Screw (316 Stainless Steel)           | Mounting the electronics enclosure cradles to the frame        
12            | M5x16 Button Head Cap Screw (316 Stainless Steel)           | Assembling the frame
7             | 8-16 Thread, 5/8" Long, Thread-Forming Screw                | Mounting the ballast to the frame                         
7             | 200g Ballast												| 

## Electronics Enclosure                                                         

Quantity      | Part																		| Usage
------------- | ----------------------------------------------------------------------------| ---------------
1             | Electronics tray with terminal blocks and ESCs installed                    |                      
1             | 4" watertight enclosure with optically clear dome installed                 |            
1             | 14 hole end cap with 3 blank penetrator, 1 Bar30 pressure sensor, 1 vent, and 1 power cable installed	|
1             | Set of tether board power wires  											| Provided power to the tether board
4             | M3x16 Socket Head Cap Screw (316 Stainless Steel)  							| Mounting the electronics enclosure to the electronics enclosure cradle
1			  | Spade to XT60 adapter   													| Connecting the PixHawk Power Module to the power terminal block
1			  | XT60 to 3.5 mm Bullet Connector adapter										| Connecting the PixHawk Power Module to the battery
4			  | 3-24 x 3/8" long self tapping screws (316 Stainless Steel)					| Mounting the tether interface board (Fathom-S or Fathom-X)
4 			  | 1/8" x 1/8" diameter spacers (Nylon)										| Mounting the tether interface board (Fathom-S or Fathom-X)
10 			  | 5 1/2" Zip Ties (Nylon)														| Cable management inside the electronics enclosure
2 			  | Pieces of two sided tape  													| Mounting PixHawk
4			  | 3-24 x 3/8" long self tapping screws (316 Stainless Steel)					| Mounting the Raspberry Pi (Advanced Electronics only)
2 			  | 1/8" x 1/8" diameter spacers (Nylon)										| Mounting the Raspberry Pi (Advanced Electronics only)
1			  | 1 1/2" long x 3/8" diameter heat shrink										| Battery cable strain relief

## Battery Enclosure

Quantity      | Part																		| Usage
------------- | ----------------------------------------------------------------------------| ------------------------
2             | Battery Enclosure Cradle (Black Anodized Aluminum w/ rubber strip)   		| Mounting the battery enclosure to the frame       
1             | 3" Watertight Enclosure 8-3/4" Long                             			|
1             | 3" Blank End Cap (Anodized Aluminum 6061)         							|
1             | 3" 4 Hole End Cap w/ 2 blank penetrators and 1 vent installed (Anodized Aluminum 6061)  |                                                              
1             | XT90 to 3.5mm Bullet Connector Adapter										| Adapting power wire connector to battery connector
4             | M4x14 Socket Head Cap Screw (316 Stainless Steel)   						| Mounting the battery cradle to the frame
4             | M3x12 Socket Head Cap Screws (316 Stainless Steel)             				| Connecting the battery cradles           

## Thrusters

Quantity      | Part													| Usage
------------- | --------------------------------------------------------|--------------
6   		  | T200 Thrusters w/ installed penetrator					|
16            | M3x16 Socket Head Cap Screw (316 Stainless Steel)      	| Mounting thrusters 1, 2, 3, and 4 to the frame
8 			  | M3x12 Socket Head Cap Screw (316 Stainless Steel)		| Mounting thrusters 5 and 6 to the frame
30            | 5 1/2" Zip Ties (Nylon)									| Routing the thruster and lumen cables

## Fairings

Quantity      | Part																	|
------------- | ------------------------------------------------------------------------| ---------------------
4             | Fairings (Blue Polycarbonate)                    						|
4             | Buoyancy Foam (R-3318 Urethane Foam)                        			|
16            | #4 Size, 3/4" Long Pan Head Self Tapping Screw (316 Stainless Steel)    | Mounting the fairings and buoyancy to the frame                               

## Tether

Quantity      | Part														| Usage 
------------- | ------------------------------------------------------------|--------------
1             | Fathom Tether w/ installed penetrator (25-300m)           	|
1             | Fathom Thimble                          					| Mounting the tether to the frame	
5             | Heavy Duty Zip Ties											| Mounting the tether to the thimble and frame            

## Tools                                                      

Quantity      | Part													| Usage
------------- | --------------------------------------------------------| ---------------
1             | Silicone Grease Tube									| Lubricate O-rings prior to installation 
1             | O-Ring Pick   											| Remove and install O-rings
1             | 2.5mm Hex Driver										| Install M3 screws 
1			  | #1 Phillips Head Screwdriver    						| Install the fairing screws 
1			  | Blue Robotics Penetrator Wrenches  
                     | Install penetrators
1			  | 1.5mm Hex Key											| Thruster dissassembly
1			  | 2mm Hex Key											   	| Change propellers
1			  | 3mm Hex Key												| Install M4 and M5 screws



# Optional Configurations

## Standard Electronics Package 

Quantity      | Part
------------- | --------------------------------------------------------
1             | Fathom-S Tether Interface Board
1             | Analog Camera with Camera Tilt
1             | 3DR PixHawk (Optional)

## Advanced Electronics Package

Quantity      | Part
------------- | --------------------------------------------------------
1             | Fathom-X Tether Interface 
1             | HD Raspberry Pi Camera with Camera Tilt
1             | Pre-loaded SD Card
1             | Battery Eliminator Circuit (for powering the Raspberry Pi)
1             | 3DR PixHawk (Optional)
1             | Raspberry Pi 3 
1 			  | PixHawk Shelf (for mounting the PixHawk to the Raspberry Pi)

## Lights

Quantity      | Part
------------- | --------------------------------------------------------
1-2           | Lumen Subsea Light w/ Mounts (Pair, Pre-Connected) (Optional)      

## What You Need for Operation that is Not Included 

There are some items necessary for operation that are not included with the kit. 

 - Analog screen for the standard BlueROV2. We recommend [this one](https://www.adafruit.com/products/2261).
 - A gamepad controller. We recommend [an Xbox360 Controller](http://www.xbox.com/en-US/xbox-360/accessories/controllers/wired-controller) or [a Logitech F310 Gamepad](http://gaming.logitech.com/en-us/product/f310-gamepad).
 - A laptop or a Windows 10 tablet. QGroundControl works on Mac, Windows 10, and Linux.
 - A battery for the BlueROV2. We recommend getting our [18AH Lithium-ion Battery](http://www.bluerobotics.com/store/electronics/batteries/battery-li-4s-18ah-r1/) or 2 or 3 of [these](http://www.hobbyking.com/hobbyking/store/uh_viewItem.asp?idProduct=56844)
 - A battery charger, we use and recommend [this one](https://hobbyking.com/en_us/turnigy-reaktor-300w-20a-ac-dc-synchronous-balance-charger-discharger-us-plug.html).   
 
# Assembling the Frame

## Mounting the Battery Enclosure to the Bottom Panel

To mount the battery enclosure to the bottom panel you will need the following parts and tools:

- 2 battery cradles 
- Thread-locker 
- Bottom panel 
- Bag with 4 M4x14 socket head cap screws and 4 M3x12 socket head cap screws
- Battery Enclosure
- 3 mm allen hex key
- 2.5 mm allen hex driver

1. Open the battery enclosure and set the bags inside of it to the side, except for the bag with 4 M4x14 and 4 M3x12 screws in it.

	

2. Apply one drop of threadlocker to the bottom of each M4x14. 

	

3. Attach that battery cradle to the bottom panel, using 4 M4x14 socket head cap screws. Be sure that the screw head is in the [counterbore](https://en.wikipedia.org/wiki/Counterbore). The bottom panel is only counterbored on one side. 

	 

4. Tighten the screws until they are flush with the bottom of the bottom panel. 

	 

5. Apply one drop of thread-locker to the end of each of the 4 M3x12 screws.

6. Grab the battery enclosure and the other battery cradle and install the 4 M3x12 screws into the cradle to clamp the battery enclosure into place. Install all four screws loosely at first and then slowly tighten them on both sides evenly.
Keep the battery enclosure approximately centered in the cradles.

	

	When you are finished tightening the screws, both sides should look similar to this.

	
	
## Assembling the Center Panels

To assemble the center panels you will need the following tools and items:

- 2 front center panels 
- 2 rear center panels 
- Thread-locker 
- The bag with 8 M4x18 socket head cap screws 
- 3 mm allen hex key 

1. Apply one drop of thread-locker to the end of each of the 8 M4x18 screws.

2. Attach one of the electronics enclosure cradle to the rear center panels. 

	
	
3. Attach the other electronics enclosure cradle to the front center panels.

	
	
## Assembling the Frame

To assemble the frame you will need the following tools and items:

- Thread-locker 
- The bag with 12 M5x12 button head cap screws 
- 2 Side Panels
- The bottom panel with the battery enclosure installed
- The front center panel assembly
- The rear center panel assembly
- 3 mm hex key
	
1. Apply one drop of thread-locker to the end of the 12 M5x16 screws.
	
2. Install the side panels to the bottom panel; the blank end cap on the battery enclosure should be on the same side as the Lumen mounting holes. Take care not to overtighten; turn with the short end of the hex key. 

	
	
3. Install the center panel assemblies to the side panels. Take care not to overtighten; turn with the short end of the hex key.

	
	
Now the ROV should look like the picture below, and it is time to move on to setting up the electronics enclosure.



# Assembling the Electronics Tray

## Advanced Overview

The electronics enclosure ships with the camera mount attached to the port side of the front panel of the electronics tray. It also ships with the power terminal blocks and the motor terminal blocks installed. 

The pictures below show orientation of the main pieces of hardware when the tray is assembled. They also point out the names of several of the important parts for assembly that will be discussed throughout the instructions.

<b> <font size="4"> Advanced Electronics Top View </font> </b> 


<b> <font size="4"> Advanced Electronics Starboard View </font> </b> 


<b> <font size="4"> Advanced Electronics Port View </font> </b> 


<b> <font size="4"> Advance Electronics Front View </font> </b> 

	
## Partially Disassembling the Electronics Enclosure

To partially disassemble the electronics enclosure you will need the following tools and items:

- Large flat head screw driver (Optional)
- The electronics enclosure assembly
- 2.5 mm allen key driver 

1. Remove the tube from the rear flange. You can twist a large flat head screwdriver in the slots if it does not pull off easily. Set the loose items that come inside the electronics enclosure to the side so you can find them easily later.

	
		
2. Remove the rear 14 hole end cap by removing the screws using the M2.5 allen driver. Place the M3x12 screws, clips, and O-ring in a safe place. 

	
	
	

## Connecting the ESC Power and Motor Wires

To connect the ESC power and motor wires, you need the following parts and tools

- 1.5 mm allen hex key
- 2.5 or 3 mm flat head screw driver
- Phillips head screw driver
- Electronics tray
- Tweezers

Here is a diagram of where the ESC power wires should go for the port and starboard side. The camera is mounted on the port side.





1. Step 1 is optional, but it definitely makes installing the power wires easier. Use the 1.5 mm hex key to remove the motor terminal blocks on both sides. 

	

2. Pass the ESC signal wires from the port side to the starboard side through the holes by the power terminal block. This will help with cable routing later.

3. Feed all black ESC power wires to the port side using the holes near the power terminal block and feed all red ESC power wires through to the starboard side. Connect the power wires to their terminal blocks. Make sure to keep the outer screw terminals open, the power wires will get connected there later. Using tweezers can help with wire routing and pushing the spades into the screw terminals.

	

4. If you did step 1, reinstall the motor terminal blocks using the 1.5 mm hex key

	

5. Connect the motor power wires to the motor terminal blocks as shown below, using your 2.5 or 3 mm flat head screw driver.

	

	
	
## Installing the Standard Electronics

If you have the Advanced Electronics, please skip to [Installing the Advanced Electronics](#installing-the-advanced-electronics)

To install the standard electronics, you need the following parts and tools:

- PixHawk Autopilot
- Fathom-S Tether Interface Board
- Bag with 4 short self tapping screws and 4 plastic spacers
- \#1 Phillips head screw driver

1. Clean the back of the PixHawk and the area on the electronics tray (starboard side) that you want to mount the PixHawk to with isopropyl alcohol.
		
2. Attach the PixHawk using the two sided tape.

	
	
	

2. 	Attach the Fathom-S Tether Interface Board to the Electronics Tray, using the self tapping screws and spacers. The tether board should mount to the port side.

	

## Installing the Advanced Electronics

If you have the Standard Electronics, please skip to [Wiring the Electronics](#wiring-the-electronics)

To install the Advanced Electronics, you need the following parts and tools:

- The Electronics Tray
- Raspberry Pi
- Raspberry Pi Shelf
- SD Card
- Bag with 4 self tapping screws and 4 spacers
- Bag with 4 self tapping screws and 2 spacers
- Fathom-X Tether Interface Board
- Two sided tape
- \#1 Phillips head screw driver

1. Install the microSD card into the Raspberry Pi.

2. Connect the camera cable from the Raspberry Pi Camera to the Raspberry Pi as shown below. To connect the camera cable, lift the tabs on the camera cable port on the Raspberry Pi, push the cable in (match the orientation in the picture), then push the tabs back down. Note the cable passing through the hole in the front panel of the electronics tray.

	

3. Attach the PixHawk shelf to the Raspberry Pi using two of the self tapping screws from the bag with four self tapping screws and two spacers. Mount the shelf in the orientation shown in the picture to ensure that you have access to the GPIO pins on the Raspberry Pi.

	

4. Attach the PixHawk to the PixHawk shelf, using the included double sided tape. Note the orientation of the PixHawk relative to the Raspberry Pi.

	

	

5. Attach the PixHawk Raspberry Pi Assembly to the Electronics Tray, using two of the self tapping screws and two of the spacers. The spacers should be between the Raspberry Pi and the tray. Make sure that the orientation matches the picture. 

	

6. Attach the Fathom-X Tether Interface Board to the Electronics Tray using the four self tapping screws and four spacers.

	

# Wiring the Electronics

## Connecting the PixHawk Power Module

To connect the PixHawk Power Module, you need the following parts and tools:

- Spade to XT60 adapter
- PixHawk Power Module
- XT60 to bullet connector adapter
- PixHawk Power Wire
- Phillips head screw driver

1. Connect the spade to XT60 adapter to the power terminal blocks. You want the Power Module to be on the port side, so route the red +16 V wire through the hole near the power terminal blocks. 

	

2. Connect the PixHawk Power Module to the XT60 connector you just installed.

	

3. Connect the XT60 to Bullet Connector adapter to the PixHawk Power Module.

	

4. Connect the PixHawk Power Wire to the PixHawk Power Module and the power port on the PixHawk.

	

## Wiring the Standard Electronics

If you have the Advanced Electronics, please continue to [Wiring the Advanced Electronics](#wiring-the-advanced-electronics)

To complete the wiring of the Standard Electronics kit you need the following items:

- The analog camera cable (included attached to the camera)
- PixHawk serial cable (included with the PixHawk)
	
1. Attach the camera wire to the "NTSC/PAL CAMERA" port on the Fathom-S Tether Interface Board.

	
	
2. Connect the serial wire (included with the PixHawk) from the "DF13 UART" port on the Fathom-S Tether Interface Board to the "Telem1" Serial Port on the PixHawk.

## Wiring the Advanced Electronics

If you have the Standard Electronics, please continue to [Signal Cable Wiring](#signal-cable-wiring)

To complete the wiring of the Advanced Electronics you need the following items and tools:

- The USB cable
- The Ethernet cable
- The tether board power wires
- The Battery Eliminator Circuit
- Phillips head screw driver

1. Connect the USB cable to the PixHawk and the Raspberry Pi as shown.

	

2. Connect the ethernet cable to the Raspberry Pi and the Fathom-X Tether Interface Board.

	

3. Connect the tether board power wires to the Fathom-X Tether Interface Board and the power terminal blocks. 

	

4. Connect the Battery Eliminator Circuit to the Raspberry Pi and the power terminal blocks. 

	

## Signal Cable Wiring

To complete the signal cable wiring you need the following items:

- A small (~2mm) flat head screw driver
- Wire cutters

1. Remove and cut the 5V line (middle wire) on 5 of the ESC signal wires. 3DR [recommends only connecting one ESC +5V output](https://pixhawk.org/users/actuators/pwm_escs_and_servos)

	i. Separate the three wires coming into the connector plug to about 2 inches away from the plug.
		
	ii. Remove the center pin from the plug by lifting up on the plastic with a small flat head screw driver.
	
	iii. Cut off the +5V line using wire cutters or scissors about an inch away from the connector plug
	
	

2. Connect the ESC signal wires to the PixHawk Main Out.

	- Channel 1: ESC 1
	- Channel 2: ESC 2
	- Channel 3: ESC 3
	- Channel 4: ESC 4 
	- Channel 5: ESC 5
	- Channel 6: ESC 6 

	<br>   See the two diagrams below for a reminder of which ESC is which.

	

	

3. Connect the camera servo signal wire to PixHawk Main Out Channel 8. Do not remove the +5V line from this connector.


	
# Changing the Propellers

To change the propellers on three of the thrusters you will need the following items and tools:

- 3 T200 Thrusters (included with ROV)
- Large (~#3) Phillips Head Screwdriver (not included)
- 2mm Allen Hex Key (included with ROV)

1. Remove 3 thrusters from their tubes. These will become Thrusters 1, 2, and 5.
	
2. Switch the propellers from the clockwise thrusters that come installed to the counter-clockwise thrusters that come along with the thrusters. Please refer to our [Changing the Propeller Tutorial](/tutorials/changing-the-propeller) for detailed instructions.

3. The next few steps will be easier if you keep the clockwise and counter-clockwise thrusters separated, and for reference the picture below shows clockwise and counter-clockwise propellers installed on thrusters.

	
	
# Installing the Cables

## Installing the Penetrators

To install the penetrators you will need the following items and tools:

- The bag with 1 black penetrator nuts, 8 red penetrator nuts, and 9 O-rings
- Silicone grease 
- 14 hole end cap with blanks, Bar30, vent, and power wire installed 
- 3 T200 with counter-clockwise thrusters 
- 3 T200 with clockwise thrusters 
- 1 set of daisy chained Lumen lights 
- 1 tether with penetrator installed
- 1 Penetrator wrench

The electronics enclosure end cap ships with 3 blank penetrators, 1 Bar30 pressure sensor, 1 vent, and 1 battery power wire penetrator installed.



If you install the remaining penetrators as shown in the diagram below, it will keep everything neat, organized and logical.


	
1. Remove 8 of the O-rings and apply Silicone grease to them. Hold on to that other O-ring, you will need it in a minute. 

	

2. Install the O-rings onto all of the thruster penetrators, the lumen penetrator, and the tether penetrator.
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

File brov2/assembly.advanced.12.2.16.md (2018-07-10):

---
layout: default
title: BlueROV2 Advanced Kit Assembly
permalink: /brov2/assembly/advanced/12.2.16
order: 1
topnavbar: brov2
nav:
- Archived Instructions: archived-assembly-instructions
- Introduction: assembly-intro
- - Safety: safety
- Required Tools: required-tools-not-included
- What's Included: whats-included
- - Frame: frame
- - Electronics Enclosure: electronics-enclosure
- - Battery Enclosure: battery-enclosure
- - Thrusters: thrusters
- - Fairings: fairings
- - Tether: tether
- - Tools: tools
- - Lights: lights
- - Leak Sensor: sos-leak-sensor
- What's Not Included: what-you-need-for-operation-that-is-not-included
- Frame Assembly: assembling-the-frame
- - Battery Enclosure: mounting-the-battery-enclosure-to-the-bottom-panel
- - Center Panels: assembling-the-center-panels
- - Frame: assembling-the-frame-1
- Electronics Overview: electronics-enclosure-overview
- Cable Installation: installing-the-cables
- - Penetrator Installation: installing-the-penetrators
- - End Cap Installation: installing-the-end-cap
- - Finishing Battery Enclosure: finishing-the-battery-enclosure
- - Optional Preliminary Vacuum Test: optional-preliminary-vacuum-test
- - Penetrator Power Wiring: installing-the-power-wires-from-the-penetrators
- - Penetrator Signal Wiring: installing-the-signal-wires-from-the-penetrators
- - Cable Routing: cable-routing
- Final Assembly: final-assembly
- - Mounting Electronics Enclosure: mounting-the-electronics-enclosure-onto-the-frame
- - Mounting Thrusters: mounting-the-thrusters-to-the-frame
- - Mounting Lights: mounting-the-lights
- - Mounting the Tether: mounting-the-tether-to-the-frame
- - External Cable Management: thruster-and-lumen-cable-management
- - Installing Fairings: installing-the-fairings-and-buoyancy
- - Ballast: mounting-ballast-to-the-frame
- Topside Setup: topside-setup
- Next Steps: next-steps

store-links:
- BlueROV2: http://bluerobotics.com/store/rov/bluerov2/

manual-links:
- Archived Assembly: /brov2/assembly/
- Software Setup: /brov2/software-setup/
- Specifications: /brov2/
- Operations Manual: /brov2/operation/

---



# Archived Assembly Instructions

- [Original Assembly Instructions](#)

# Assembly Intro

The BlueROV2 kit comes almost ready to dive. The assembly can be completed with basic hand tools; no soldering or potting is required. We have included a couple of the tools to make assembly and regular use as easy as possible.

## Safety 

<i class="fa fa-exclamation-triangle fa-fw fa-2x text-warning"></i> When working with electricity, especially in water, always practice caution. Always ensure that connections are secure and watertight. Keep your body away from spinning motors and propellers.

<i class="fa fa-exclamation-triangle fa-fw fa-2x text-warning"></i> When working with silicone grease and threadlocker, take care to minimize skin contact. Wear protective nitrile or PVC gloves when handling.

# Required Tools (Not Included)

- \#2 Phillips head screwdriver 
- Wire cutters or scissors (for cutting zip ties)
- Medium-strength (blue) threadlocker such as [Loctite 243](https://www.amazon.com/Loctite-1330799-Resistant-thread-locker-6-milliliter/dp/B004L439FE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)
- Isopropyl alcohol or isopropyl alcohol wipes
- Vacuum pump such as [this one](https://www.amazon.com/HFS-Brake-Bleeder-Vacuum-Tuner/dp/B00NP60URE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)
- 2 mm flat head screw driver

# What's Included

## Frame

Quantity      | Part														| Usage
------------- | ------------------------------------------------------------| ----------------------
2             | Front center panel (1/2" thick black HDPE)        			|    
2             | Rear center panel (1/2" thick black HDPE)           		|     	       
1             | Bottom panel (1/2" thick black HDPE)                       	|  
2             | Side panel (3/8" thick black HDPE)                       	|
2             | Enclosure Cradle (4" Series) (black anodized aluminum)  	| Mounting the electronics enclosure to the frame
8 			  | M4x18 socket head cap screw (316 stainless steel)           | Mounting the electronics enclosure cradles to the frame        
12            | M5x16 button head cap screw (316 stainless steel)           | Assembling the frame
7             | 8-16 thread, 5/8" long, thread-forming screw                | Mounting the ballast to the frame                         
7             | Ballast Weight (200g, 7 oz)									|
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

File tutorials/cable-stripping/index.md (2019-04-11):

---
layout: default
title: Wire Stripping Blue Robotics' Cable
permalink: /tutorials/cable-stripping/
order: 1
nav:
- Introduction: introduction
- - Safety: safety
- - Tools You Need: tools-you-need
- Video Tutorial: video-tutorial
- Instructions: instructions
- - Step 1 - Stripping the Jacket: step-1-stripping-the-jacket
- - Step 2 - Stripping the Conductors: step-2-stripping-the-conductors

redirect: https://www.bluerobotics.com/learn/cable-stripping/
---

# Introduction

Blue Robotics' thrusters and BlueESC come with tough urethane jacketed cable for reliable performance underwater. It can be a little tricky to strip the jacket from the cable but these steps should make it simple!
 
## Safety

<i class="fa fa-exclamation-triangle fa-fw fa-2x text-warning"></i> When working with tools, always use caution. This tutorial is provided as guidance and should be followed at your own risk.

## Tools You Need

* Sharp knife (razor blade or X-Acto knife work well)
* Protective glove
* Wire strippers with slot for 18 AWG wire

# Video Tutorial

<iframe width="700" height="393.75" src="https://www.youtube.com/embed/jNYPrN3rj5k" frameborder="0" allowfullscreen></iframe>
<br />

# Instructions
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

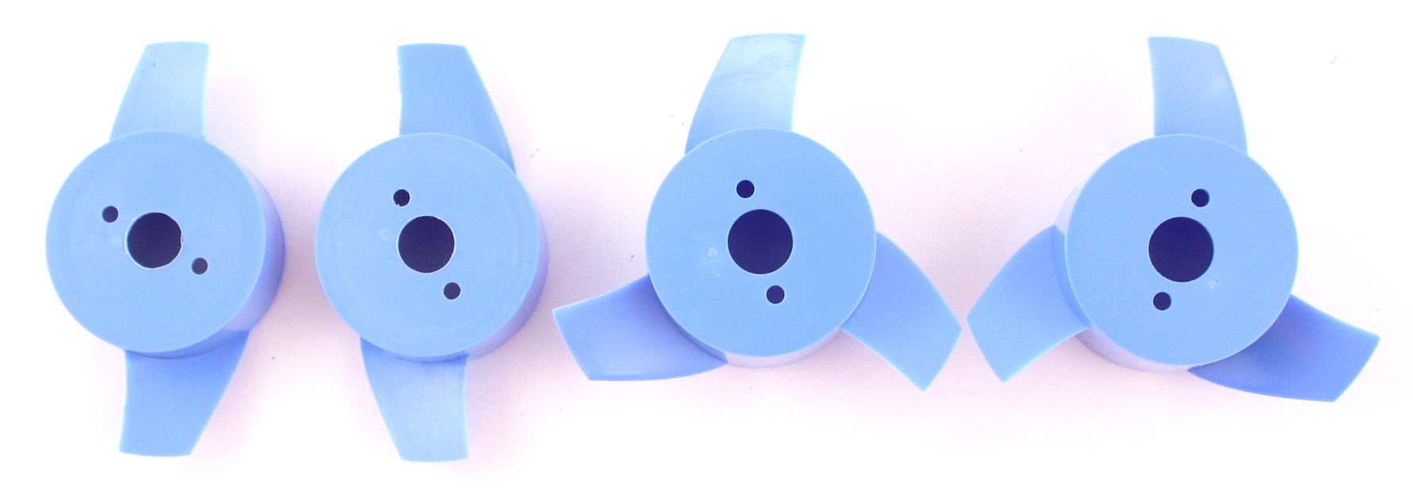
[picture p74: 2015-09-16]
assets/images/tutorials/changing-a-propeller/all-propellers.png

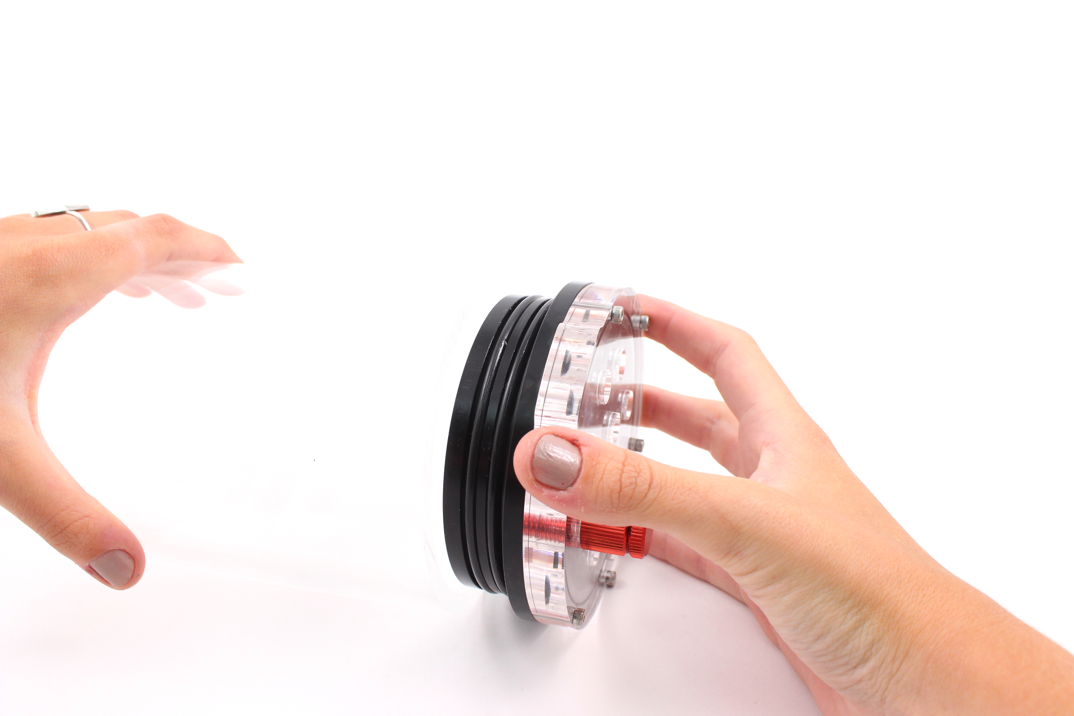
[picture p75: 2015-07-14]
assets/images/tutorials/WTE/step-5.png

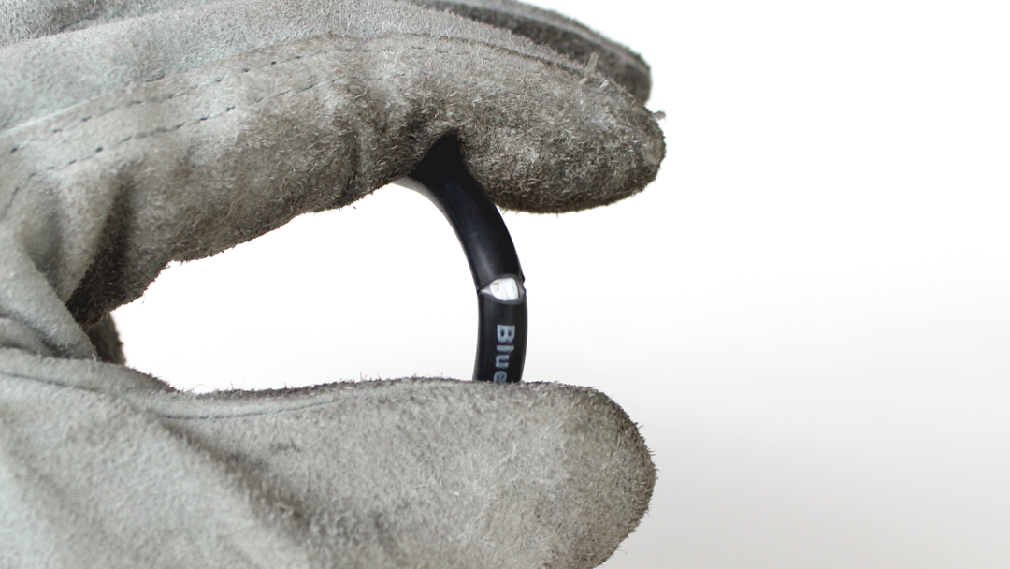
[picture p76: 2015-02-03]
assets/images/tutorials/wire-stripping/wire-strip-5.png

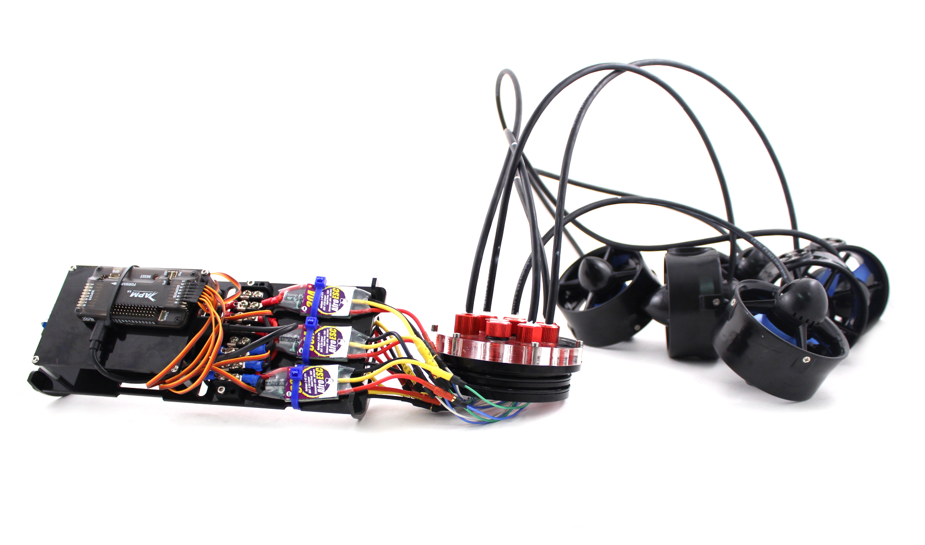
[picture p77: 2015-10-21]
assets/images/tutorials/bluerov-manual/BR-1.png

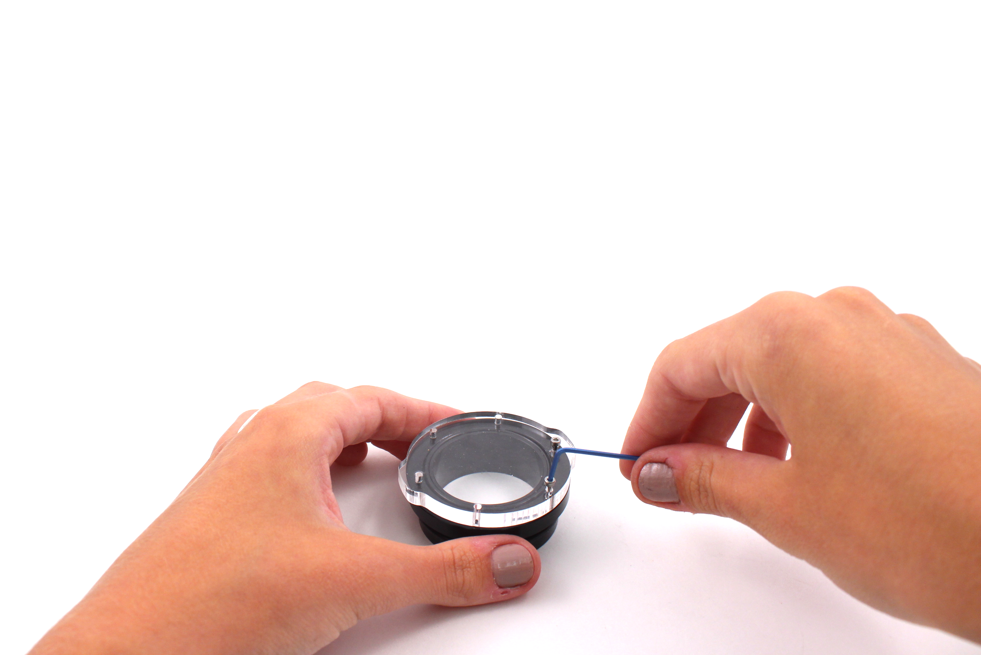
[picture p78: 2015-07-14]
assets/images/tutorials/WTE/2-step-3.png

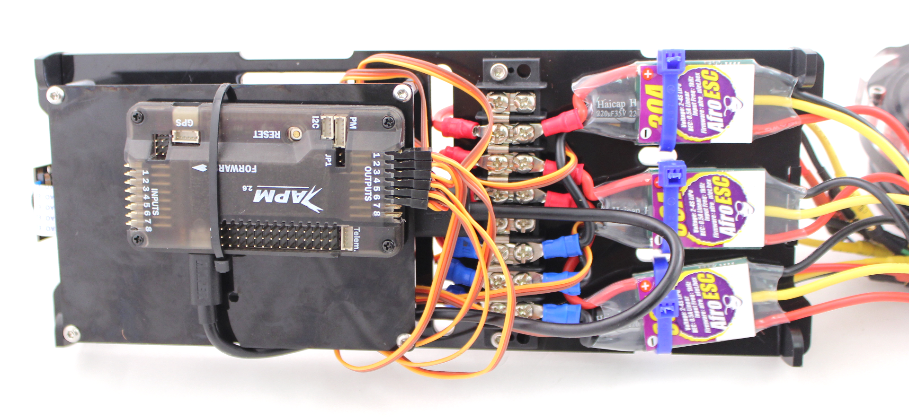
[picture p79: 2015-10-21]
assets/images/tutorials/bluerov-manual/BR-2.png

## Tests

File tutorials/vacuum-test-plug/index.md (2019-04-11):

---
layout: default
title: Using the Vacuum Plug
permalink: /tutorials/vacuum-test-plug/
order: 1
nav:
- Introduction: introduction
- Attaching the Vacuum Plug to the Pump: attaching-the-vacuum-plug-to-the-pump
- Testing the Test Setup: testing-the-test-setup
- Testing the Enclosure: testing-the-enclosure

redirect: https://www.bluerobotics.com/learn/using-the-vacuum-test-plug/
---

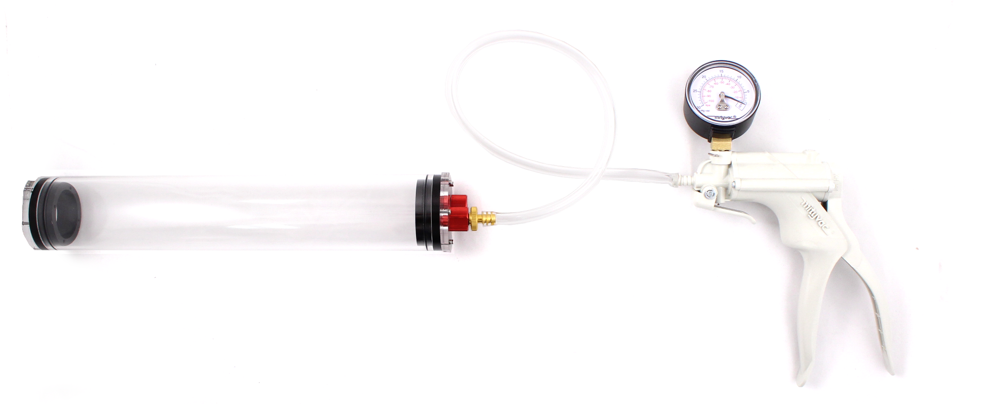
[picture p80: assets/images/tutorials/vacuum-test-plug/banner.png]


# Introduction

This part allows you to vacuum test enclosures through the standard vent, ensuring a watertight seal. It fits to a 1/4" hose and works great with most hand-operated vacuum pumps for in-the-field testing!

## Tools You Need

* Hand-operated vacuum pump
* [Vacuum test plug](https://www.bluerobotics.com/store/tools/vacuum-plug/) 
* [Silicone grease](https://www.bluerobotics.com/store/tools/tool-silicone-grease-10g-r1)

# Attaching the Vacuum Plug to the Pump

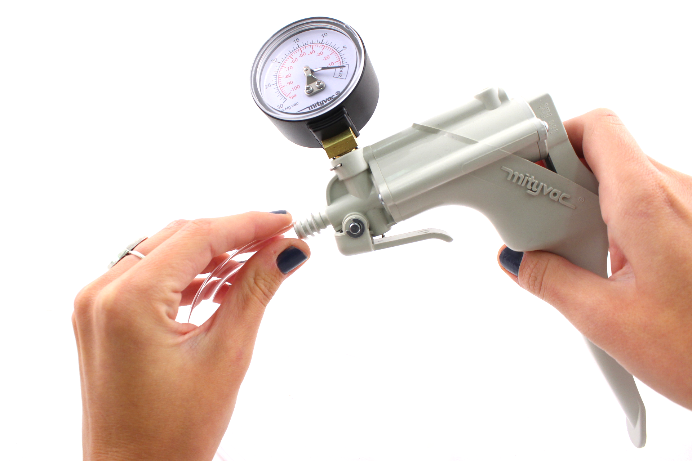
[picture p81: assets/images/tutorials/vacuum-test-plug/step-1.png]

1. Attach clear vacuum hose to the pump (refer to instructions for your pump).
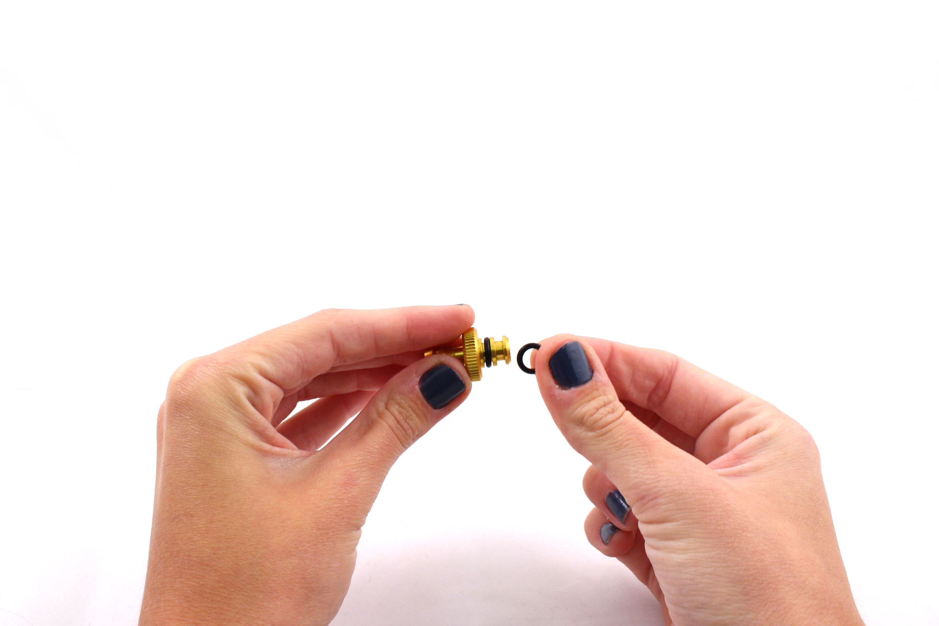
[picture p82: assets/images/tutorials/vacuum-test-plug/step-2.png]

2. Install O-rings on the vacuum plug, lubricating lightly with silicone grease before installation.
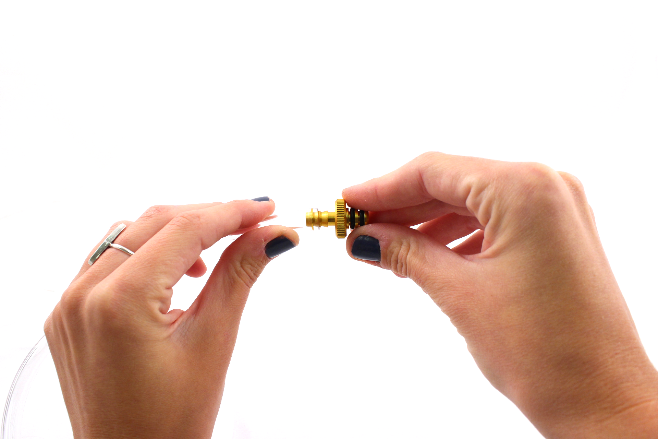
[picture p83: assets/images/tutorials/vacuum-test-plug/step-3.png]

3. Insert the barbed end of the vacuum plug into the vacuum hose.

# Testing the Test Setup

Before testing the enclosure, it's a good idea to test the pump, hose, and vacuum plug alone to make sure that there are no leaks in the pump, the vacuum gauge, or the hose connections. The vacuum plug comes with a rubber stopper that makes this easy! The following describes how to test these parts (i.e. "testing the test setup").

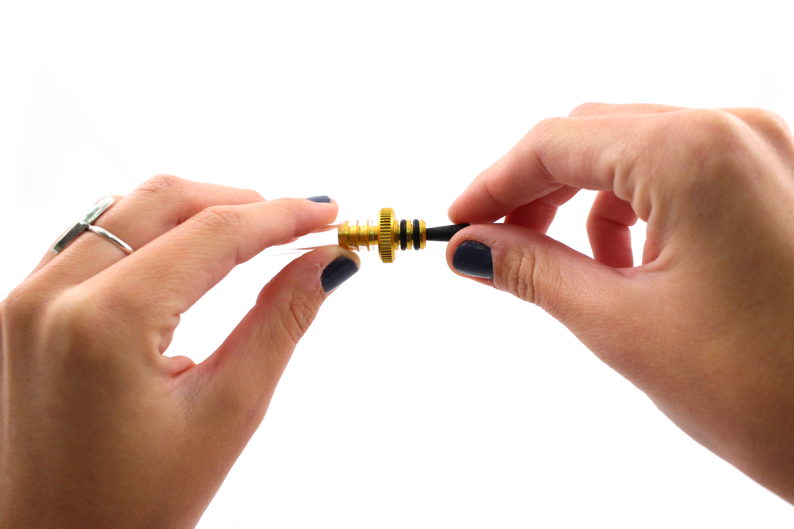
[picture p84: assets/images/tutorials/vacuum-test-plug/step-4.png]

1. First, insert the rubber plug into the hole on the vacuum plug to seal it up.
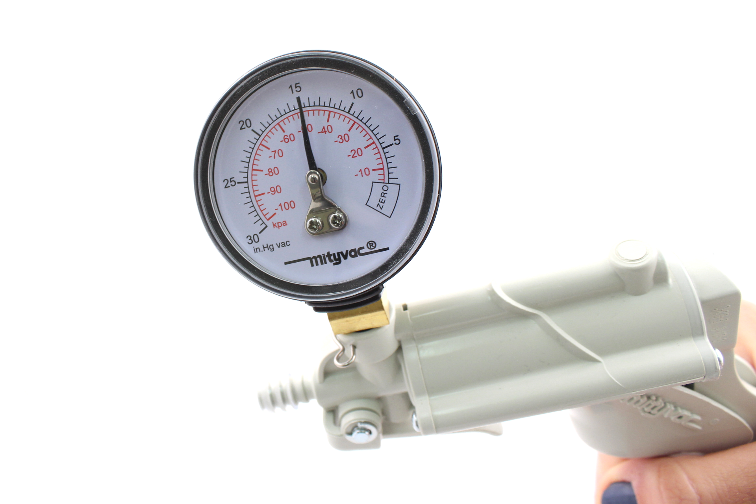
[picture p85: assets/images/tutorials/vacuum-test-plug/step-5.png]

2. Pump the hand pump to approximately 400 mmHg (about 15 inHg), and monitor for about 10-15 minutes, making sure that the pressure does not decrease by more than 10 mmHg (0.5 inHg).   
3. If successful, this test setup is ready to use. If not, check the following:   

* Proper hose connections on the pump and on the vacuum plug
* The vacuum pump and vacuum gauge (You can test the pump by removing the hose and using the rubber stopper to plug the hole.)

# Testing the Enclosure

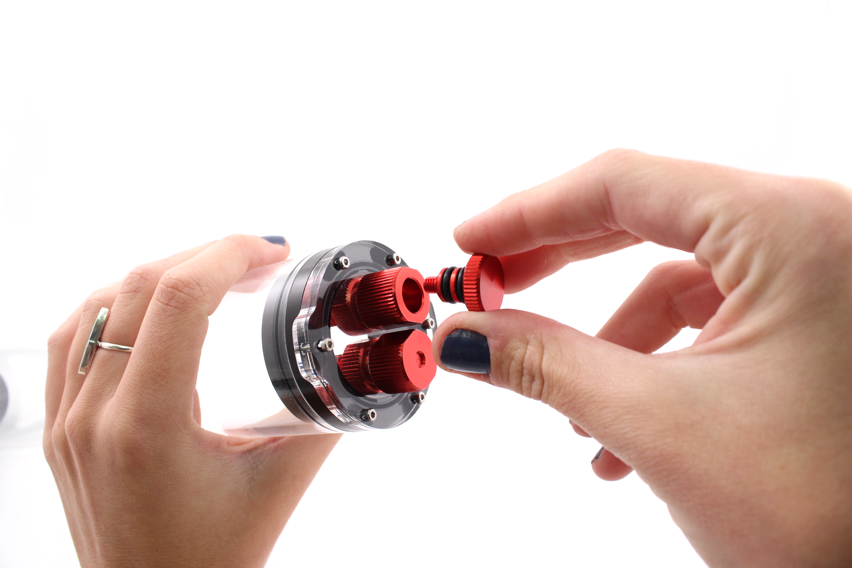
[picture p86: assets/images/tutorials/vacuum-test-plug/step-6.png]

1. First, remove the sealing plug from the vent on the watertight enclosure.
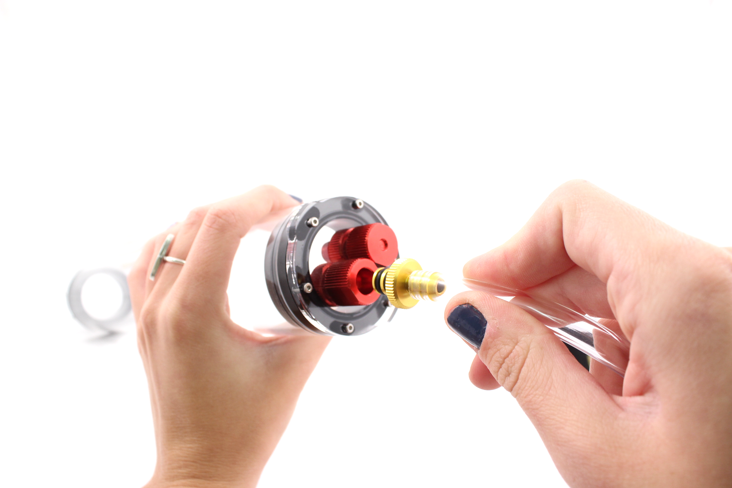
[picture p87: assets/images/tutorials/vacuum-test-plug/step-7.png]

2. Insert the vacuum plug attachment. 

3. Pump the hand pump, removing air and decreasing the pressure inside the enclosure to approximately 400 mmHg (about 15 inHg). This will take quite a few pumps - roughly 38 pumps for an empty 2" enclosure, 85 pumps for an empty 3" enclosure, and 152 pumps for an empty 4" enclosure (using a Mityvac hand pump).      
4. Monitor the gauge for about 10-15 minutes and make sure the vacuum pressure does not decrease by more than 10 mmHg (0.5 inHg). 

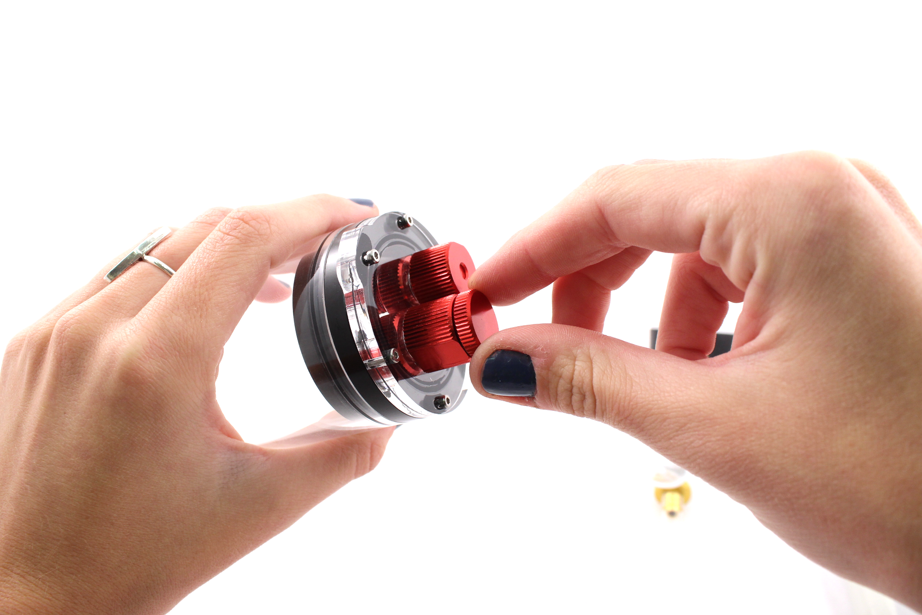
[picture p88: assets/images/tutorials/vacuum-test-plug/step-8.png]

5. If successful, remove the test plug, and replace with the original vent plug. If you find a leak, check the following: 

* Hair, dust, or other obstructions of the O-ring seals
* Loose cable penetrators
* Scratches on the inside of the tube

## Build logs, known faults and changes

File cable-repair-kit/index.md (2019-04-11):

---
layout: default
title: Cable Repair Kit Tutorial
permalink: /cable-repair-kit/
order: 1
nav:
- This Page Has Moved: this-page-has-moved

store-links:
- Cable Repair Kit: https://www.bluerobotics.com/store/tools/tool-kit-cable-repair-r1-rp/
- Coax Seal: https://www.bluerobotics.com/store/tools/tool-coax-seal-0-5in-60in-r1-rp/
- Silicone Tape: https://www.bluerobotics.com/store/tools/tool-silicone-tape-1in-10ft-r1-rp/
- Acetone Wipes: https://www.bluerobotics.com/store/tools/potting-acetone-wipes-qty10-r1-rp/

manual-links:
- Potting Compound: /potting

redirect: https://www.bluerobotics.com/learn/cable-repair-kit-guide/
---

# This Page Has Moved

We're glad you ended up here but this page has moved! All of our guides and tutorials are now on our main website at [bluerobotics.com/learn](http://bluerobotics.com/learn/). You can find this particular tutorial [here](https://www.bluerobotics.com/learn/cable-repair-kit-guide/).

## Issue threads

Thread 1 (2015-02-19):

BESC30-R1 CAD File Missing

thomasshim93, 2015-02-19:
Hi, I wanted to download the CAD file for the Basic ESC, but all the links are broken.

rjehangir, 2015-02-19:
Hi Thomas,

Good catch. We'll try to have that file updated within a few days. Please check back then.

Best,

Rusty

rjehangir, 2015-03-09:
Sorry for the delay, but the files have been added and the links fixed!

-Rusty

Closed 2015-03-09.

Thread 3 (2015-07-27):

Water tight enclosure

vinothglitch, 2015-07-27:
Hi, It would be really helpful for marine robotics researchers if you could widen your catalogue of water tight enclosures with increased OD. I require an enclosure with OD of 10" and depth rating of 100m for one of my underwater robots. Thanks.

rjehangir, 2015-07-28:
Hi - I agree and we are considering doing this. Thanks for your input!

-Rusty

Closed 2016-01-02.

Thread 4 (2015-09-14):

BlueESC

gaitskell, 2015-09-14:
The manual doesn't explain what the red and blue LED's indicate on the integrated BlueESC. Also what does it mean when it beeps every few seconds?

I am able to read I2C data from the BlueESC but am unable to get prop spinning when writing I2C. Do you have any debug suggestions? Do you have to use PWM stop signal to activate motor, prior to being able to use I2C? I assume not? Do you have some I2C Python SBUS examples you could post to make sure I'm using your desired conventions? Thanks
Rickg@gaitskell.com

gaitskell, 2015-09-14:
Ok - so we figured it out by trial and error. I2C requires a write THROTTLE 0 for safety before a write THROTTLE 50 (finite speed). And you have to write <= 0.5 secs to avoid safety shutdown (which is a good feature). We filmed a video of the basic logic of operation and will post it on YouTube. Obviously, it would be great to get the online docs to include these aspects of I2C operation.

Closed 2015-09-14.

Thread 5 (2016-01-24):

Add calculators to "getting started" page with appropriate images

rjehangir, 2016-01-24:

jaxxzer, 2019-03-19:
@rjehangir are the calculators where you want them to be today?

Williangalvani, 2019-03-25:
Closing this as we are using another tool to track issues with the new docs.

Closed 2019-03-25.

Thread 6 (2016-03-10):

T200 Advance ratio

Txon, 2016-03-10:
Hi friends:

I'm into a design that will use your T200 thruster. Albeit you've provided a lot of information, I'd like to know a few details about the testing conditions related to the published curves.

May I know which "free flow speed" was used for the Thrust curves plotting ? Or are those curves obtained in static conditions ?

I need that data in order to achieve some hidrodynamic goals.

Thanks in advance and ... kind regards

rjehangir, 2016-05-23:
Hi Txon, sorry we never answered this! The curves on our documentation were all collected at near-static conditions. We don't have any data for thrust with non-zero flow speed.

Best, Rusty

Txon, 2016-05-25:
Hi Rustom, better late thern never. Thanks for your answer. I'll try to
perform some calculations for non-zero free stream speed.

Thanks again.

2016-05-23 2:48 GMT+02:00 Rustom Jehangir <notifications@github.com>:

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

Closed 2019-03-19.

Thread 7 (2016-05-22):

ROV

sudeera193, 2016-05-22:
Hi,

You have mentioned that the ROV has 200 thrusters. But in the image it shows T100 propellers. so actually what are the thrusters you used for the blue ROV.

rjehangir, 2016-05-22:
Hi Sudeera - the BlueROV uses T200 thrusters. The images were taken of a prototype with T100 thrusters, unfortunately. I have added a note about that in the documentation.

Closed 2016-05-22.

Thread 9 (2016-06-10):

New I2C adress after update

agademer, 2016-06-10:
default I2C address for the blueESC is 0x29

after update the firmware with the "blueesc_id1.hex" file, it would be intuitive that the new I2C address should be 0x01... but in reality it is : 0x29 + 1 = 0x2A !

You may add this unwritten rule to the documentation page to avoid some pain (and panic) to the futur users :)

To find the address of an unknown BlueESC we have made the following code that we are happy to share with the community

[I2CSeekAddress.zip](https://github.com/bluerobotics/bluerobotics.github.io/files/308759/I2CSeekAddress.zip)

Thank you for your beautiful motors :)

jaxxzer, 2019-03-19:
Closing with `wontfix` as the BlueESC is no longer in production.

Closed 2019-03-19.

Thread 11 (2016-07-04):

Link to hex for flashing Basic ESC is not working

Krzysaker, 2016-07-04:
At http://docs.bluerobotics.com/besc/#advanced link for **Basic ESC Firmware (BESC30-R1)** (http://docs.bluerobotics.com/besc/firmware/afro_nfet_besc30_r1.hex) returns 404 error.

rjehangir, 2016-07-04:
Thanks for catching this! It's fixed.

Closed 2016-07-04.

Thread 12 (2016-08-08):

BlueROV2 CAD files missing

markwilkie, 2016-08-08:
The links to the CAD files here (http://docs.bluerobotics.com/brov2/) don't actually point to any CAD files.

rjehangir, 2016-08-08:
Hi Mark,

Thanks for pointing that out. We've got the files on GrabCAD and we're going to change the page to point to those files instead so that our servers don't get hammered with the relatively large file size.

Here's the link where you can download them: https://grabcad.com/library/bluerov2-1

-Rust

Closed 2016-08-08.

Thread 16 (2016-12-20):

Pressure/Depth calculator doesn't work

bbalaji-ucsd, 2016-12-20:
http://docs.bluerobotics.com/calc/pressure-depth/?waterType=fresh#learn-more

Does not show output

rjehangir, 2016-12-20:
Thanks! Fixed it.

Closed 2016-12-20.

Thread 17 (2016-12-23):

Doc hasn't a detailed description of LED indicator light behavior?

bnwn, 2016-12-23:

rjehangir, 2016-12-24:
@bnwn Thanks for posting this issue. Are you talking about the LED indicator on the BlueESC, Basic ESC, something else? We can definitely add this.

bnwn, 2016-12-26:
Hi Rustom,
 i use the BlueESC. If i want to change firmware for esc with simonk bootloader, in addtion to Turnigy USB Linker, what USB linker/ programmer i can also use??
Grateful for yo reply.

jaxxzer, 2019-03-19:
Closing with `wontfix` as the BlueESC is no longer produced.

Closed 2019-03-19.

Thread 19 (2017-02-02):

Link to Solidworks files not working

twharrison, 2017-02-02:
http://docs.bluerobotics.com/tutorials/cable-penetrator/

The .zip folder download links (all three) are not functioning.

rjehangir, 2017-02-02:
@twharrison - Thanks for pointing this out! It actually affected all CAD models downloads across the docs after we migrated our website last week. It's fixed now!

Closed 2017-02-02.

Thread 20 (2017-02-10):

Suggestion- Vacuum test

DTopland, 2017-02-10:
The vacuum test for the telemetry can should be done **between** the two o-rings, not the entire can. When testing the whole can you need a huge leakage to be able to read the leakage on the gauge. A small leakage like a hair or some rag on the o-rings will not bee seen unless the test last for very extended periods.
**Measuring between the o-rings test both o-rings.** Today's test only require one o-ring to be OK in order to pass the test.
It is not a question IF but WHEN you forget to put back the vacuum test cap. If the vacuum test vent goes between the O-rings, the area between the two o-rings will be flooded but not the telemetry can, unless the inner o-ring fails. In that case the technician should have experienced that the vacuum test failed prior to put the vehicle in water.

jaxxzer, 2019-04-02:
You are correct that passing a pressure test with both seals installed does not _necessarily_ mean that the integrity of both seals is maintained, only that at least one of them is. I don't know if it would be possible to test both seals individually without invalidating the results by unsealing the container between tests.

The redundancy provided by the double o-ring seal makes it twice as likely that you will pass the test, which is still useful, and still provides redundancy at depth when both seals are in fact maintained.

In practice, the radial o ring seals very rarely fail.

Closed 2019-04-02.

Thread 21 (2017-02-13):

Materials used

Joel-George, 2017-02-13:
A brief description about the materials used( for ex: material used for cable penetrators) can be provided for a better understanding.

jaxxzer, 2019-04-02:
@bluerobotics/engineering

Can we make this available in the technical details tab on applicable items?

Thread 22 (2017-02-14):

SOS Leak Sensor

jnewm13, 2017-02-14:
The recommended location shown in the diagram and the location shown in the pictures don't match.

Williangalvani, 2019-03-25:
I just checked and it is still wrong.
The documentation issues are being tracked internally. I moved this there.

Closed 2019-03-25.

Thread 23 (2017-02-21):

Blue Robotics Battery Calculator

hailey2594, 2017-02-21:
I am trying to use the battery calculator on the Blue Robotics website and it is not working. I have tried using 2 different computers and it is not working on either.  I used this tool about 2 months ago and it was working but now I cannot get it to work.

Thank you

rjehangir, 2017-02-21:
Thanks, it's been fixed!

Closed 2017-02-21.

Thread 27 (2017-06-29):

No 'TX mode' selection available in QGroundControl

pvazteixeira, 2017-06-29:
In the 'Joystick/Gamepad Calibration' Step of the manual, step 2 states:

`Ensure the ‘TX Mode’ selection is set to 3`

In QGroundControl v3.1.3 there is no TX Mode selection GUI element.

Williangalvani, 2019-03-25:
It works fine in master:
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

Closed 2019-03-25.

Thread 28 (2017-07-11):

Clarify motor direction setup

jaxxzer, 2017-07-11:
Many miss this or mess it up.

jaxxzer, 2019-03-20:
This has been largely improved since the issue was opened. The motor test page in QGC clears it up.

Closed 2019-03-20.

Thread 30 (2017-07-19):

BROV2 kit assembly page difficult to view

jaxxzer, 2017-07-19:
The text on the page bounces around for a couple of minutes as all of the many images load.

We should compress/resize the images so they load faster, or have the image containers initialize to the correct height before the image is loaded.

rjehangir, 2017-07-19:
Good idea. There are a few ways to do this I think:

- Add javascript to put each `img` tag into a `div` with set height
- Compress the images, probably changing them to jpegs would make a huge difference
- Add a "lazy load" javascript library so that pictures only load when you scroll to that part of the page but are properly sized already, which would minimize loading time.

jaxxzer, 2019-04-02:
This is much better behaved for me today, due to faster response from the server. I'm not sure how it will look on a low bandwidth connection however, and if something can still be done there in terms of not bouncing text around while things load.

jaxxzer, 2019-04-02:
I think the effort will outweigh the benefit at this point, so will close in that spirit.

Closed 2019-04-02.

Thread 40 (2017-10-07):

CAD models are missing for 6" and 8" end caps with 15 and 25 holes

rjehangir, 2017-10-07:

Williangalvani, 2019-04-02:
This issue got moved to the Product Page Issues List.

Closed 2019-04-02.

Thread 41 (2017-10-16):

Update SOS Doc QGC Pics

dheideman, 2017-10-16:
SOS Leak Sensor documentation still uses screen captures from old QGC version, may be difficult to follow.

http://docs.bluerobotics.com/sos/

Williangalvani, 2019-03-25:
As we are moving the docs, this is now being tracked elsewhere

Closed 2019-03-25.

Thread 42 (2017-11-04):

Add connection diagram to electronics package product documentation

jaxxzer, 2017-11-04:

les1950, 2017-11-23:
This is for ROV2 - Missing is wire diagram of all connections. Pictures are not sufficient as they leave too many questions I cannot find answers.
For I2C (http://docs.bluerobotics.com/level-converter/) - no info which pins to use on UNO. Picture not showing the pins.
These small things are just annoying for a kit (very nice) value over $4k if fully loaded.

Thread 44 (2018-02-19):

Motors won't spin

henrys-code, 2018-02-19:
Hello,
I purchased 6 of your new model of ESCs and have them connected to a pixhawk with ardusub firmware 3.5.2 stable version git revision 07f2d5ac, which is connected over usb to an nvidia jetson tx2 which is running mavproxy to connect over ethernet to a laptop running qground control, which has a logitech f310 controller plugged in. I am able to arm and disarm the controller with the start and select buttons but when I move the joysticks the motors do not spin. Do the ESCs need calibrated? I have tested them with a servo tester and they all work fine and spin the motors, but they don't work when connected to pixhawk. Any help would be great, thanks!

Williangalvani, 2019-03-25:
Please keep support questions to https://discuss.bluerobotics.com/ or support@bluerobotics.com

Closed 2019-03-25.

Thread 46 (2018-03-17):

Update BROV2 Camera in Assembly Doc

kklemens, 2018-03-17:
Update BOM to reflect that the Low-Light HD USB Camera is now standard instead of the RPI Cam 2.

Closed 2018-05-04.

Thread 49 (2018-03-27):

Broken Link

tuialexandre, 2018-03-27:
The following link isn't working:

_Detailed Lithium-ion Storage Information_

From the following page:
http://docs.bluerobotics.com/batteries/

AdamBlueR, 2018-03-27:
Batterybro website appears to be temporarily down, will update link if not online in 48 hours.

AdamBlueR, 2018-04-06:
Batterybro website back up.

Closed 2018-04-06.

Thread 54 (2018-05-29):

Include cables with boards

jaxxzer, 2018-05-29:
Serial converters, and Fathom S should come with jumper wires and df13/gh connectors. We should provide all the cabling necessary to connect to any board interface.

rjehangir, 2018-05-29:
Do you think the new serial converters should come with header pins? Daniel and I have been discussing this. Our recommended uses will use the JST-GH connectors.

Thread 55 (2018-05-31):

Incorrect Fathom Slim Resistance

dheideman, 2018-05-31:
The resistance of the Fathom Slim tether should be the same as the Fathom Tether.

rjehangir, 2018-05-31:
@dheideman The wires for the 4 pair tether are actually slightly oversized for 26AWG. They're something like 25.8AWG. Because of that, I'd actually expect the two tethers to have slightly different resistance per meter.

dheideman, 2018-05-31:
@rjehangir That's... annoying...

Despite that, the Fathom Slim resistance in the docs still appears to be incorrect.  This is what I found:
Slim: 0.128 Ω/m
Regular: 0.122 Ω/m

jaxxzer, 2019-03-26:
Can this be closed @dheideman?

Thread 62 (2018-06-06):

Add missing cad models

jaxxzer, 2018-06-06:

jaxxzer, 2018-06-06:
Some that we need are here: https://github.com/bluerobotics/bluerobotics.github.io/pull/60

Bobsthinking, 2018-06-17:
Hi! can i do all of cad models that are missing?

kklemens, 2018-08-28:
Every product now has a 2D Drawing and 3D Model, the big ones are on GrabCAD.

Closed 2018-08-28.

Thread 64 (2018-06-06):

Doc issue: bar30 taring

jaxxzer, 2018-06-06:
Common question: My pressure sensor is not reading zero in air, is it broken?

Answer:
This is the result of an offset. The measurement needs to be 'tared' like a kitchen scale. Subtract the steady offset in software to get the correct measurement.

Also, depends on atmospheric pressure.

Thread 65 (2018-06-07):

brov2: add windows game center doc for center joystick button

jaxxzer, 2018-06-07:
Resolve this type of thing: https://discuss.bluerobotics.com/t/joystick-function/2702

Closed 2018-06-13.

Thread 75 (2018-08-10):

Git merge mess on Basic ESC R3 docs page

rjehangir, 2018-08-10:
Messed up merge commit.

Williangalvani, 2019-03-25:
Closing this because the new product page is ok:
https://www.bluerobotics.com/store/thrusters/speed-controllers/besc30-r3/

Closed 2019-03-25.

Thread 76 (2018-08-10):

Thruster Commander: Add voltage and frequency output information

patrickelectric, 2018-08-10:

Williangalvani, 2019-04-03:
Moved to "Product Page Issues List"

Closed 2019-04-03.

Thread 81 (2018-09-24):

Raspberry pi pwm shield thruster examples

jaxxzer, 2018-09-24:
This is quite a common request.

rjehangir, 2018-09-24:
@jaxxzer Daniel is also very interested in handling this one from Japan.

dheideman, 2018-09-24:
It'll be at least a week before I would be able to work on this.

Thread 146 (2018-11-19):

BROV2: Add note about configuring low voltage failsafe to software setup

jaxxzer, 2018-11-19:

Williangalvani, 2019-04-03:
PR open https://github.com/bluerobotics/ardusub-gitbook/pull/61

Closed 2019-05-07.

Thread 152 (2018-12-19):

Power sense module doc and tutorials say xt60, but it comes with 3.5mm bullets

jaxxzer, 2018-12-19:

patrickelectric, 2019-03-19:
is this still valid ?

kklemens, 2019-03-19:
Yes, haven't gotten to it yet.

Williangalvani, 2019-03-25:
Closing the issue here, it is now being tracked somewhere else.

Closed 2019-03-25.

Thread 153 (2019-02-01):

Pixhawk channel 7 already used

mcclainrt, 2019-02-01:
When assembling my ROV2 the instructions say to install the lumen control wire to channel 7 of the pixhawk. This channel is already used by what appears to be the camera servo. Can the lumen go into a aux port?

Closed 2019-02-04.

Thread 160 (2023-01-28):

Fathom ROV Tether connection to Fathom-X Tether Interface Board

kizunaiver, 2023-01-28:
Hey Good Evening,

We are in college. Doing a ROV project. So we ended up buying most of the electronic components individually. And now we are having trouble wiring the whole system.

The obstacle we are facing currently is, understanding tether's end wires. What are their applications? More specifically, how would I connect the tether to the fathom-X board?

We also tried researching more about schematic diagram of the the whole blueROV2. We couldn't pinpoint a single reliable source so far. from 2018 we found a discussion with the same problem. But the solution page/website no longer exists.

Any help is greatly appreciated.
Thank you.

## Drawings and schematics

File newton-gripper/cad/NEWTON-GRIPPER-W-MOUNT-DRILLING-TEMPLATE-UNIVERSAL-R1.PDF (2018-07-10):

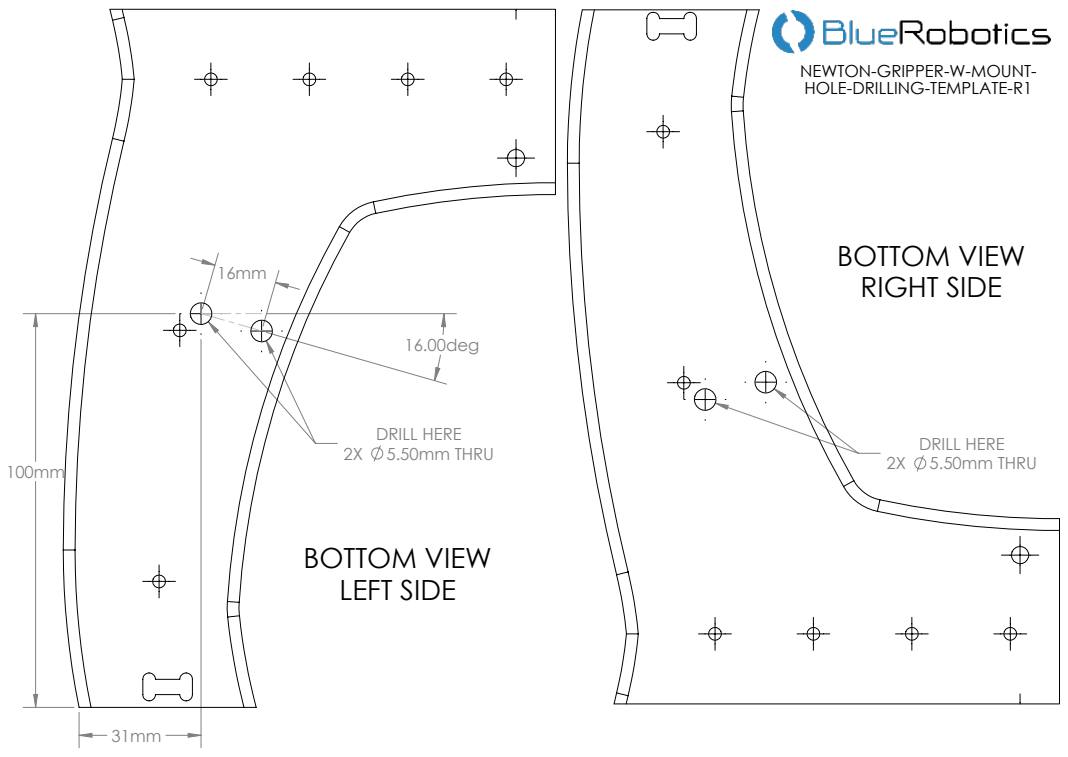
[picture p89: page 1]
DRILL HERE 2X 5.50mm THRU; BOTTOM VIEW LEFT SIDE; BOTTOM VIEW RIGHT SIDE

NEWTON-GRIPPER-W-MOUNT-
HOLE-DRILLING-TEMPLATE-R1

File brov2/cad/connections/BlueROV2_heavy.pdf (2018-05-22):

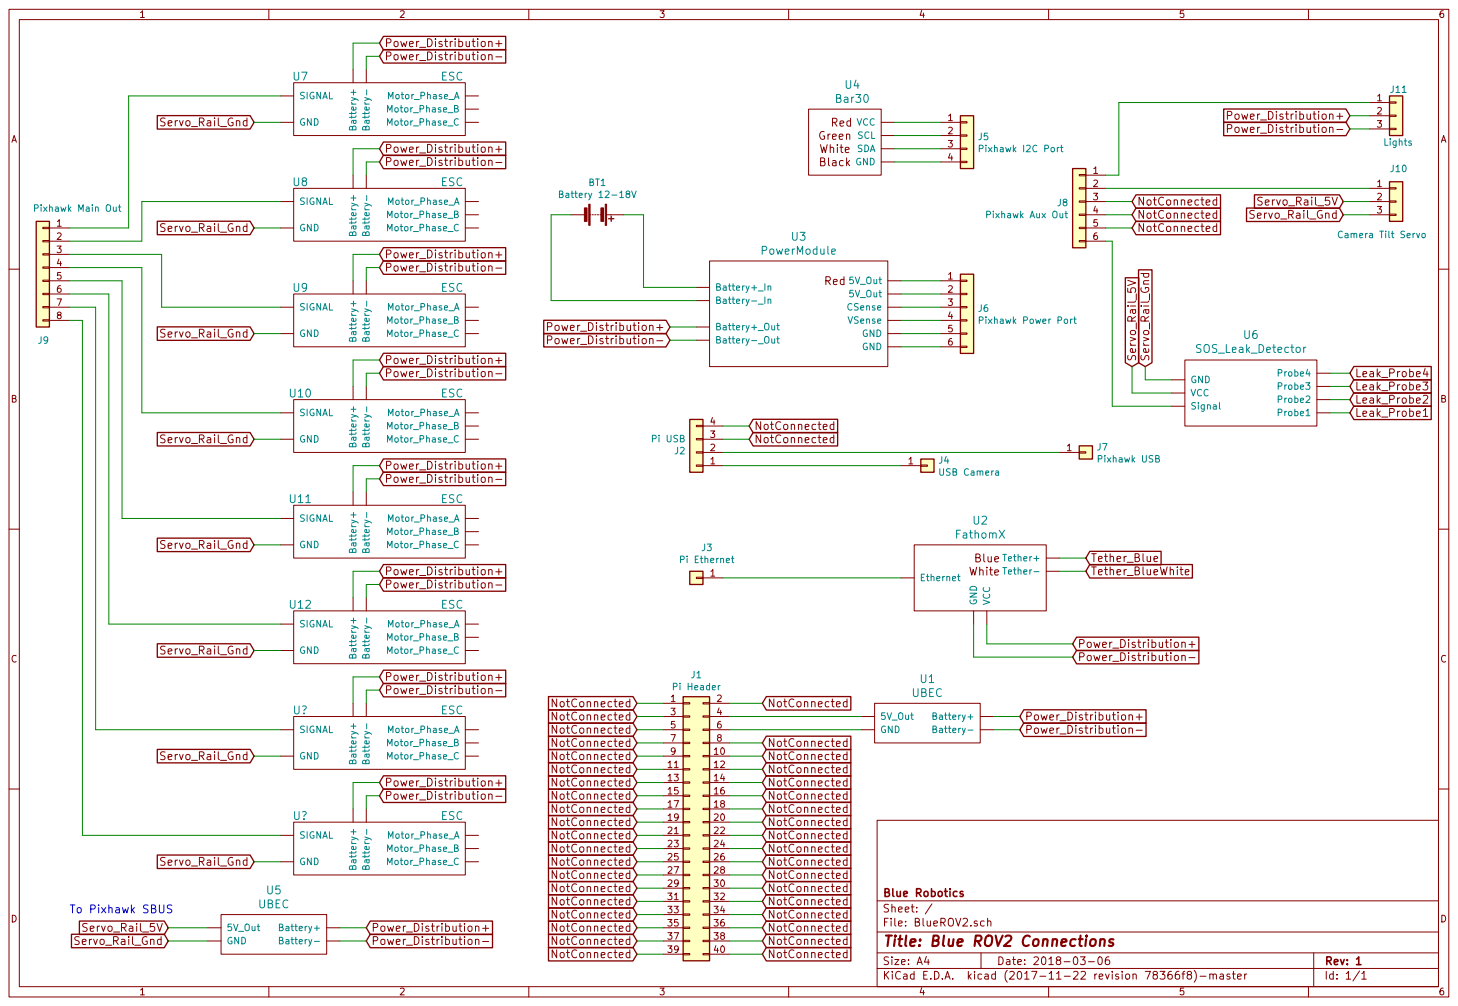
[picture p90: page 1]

VSense U3 PowerModuleBlack Green Red White GND

Tether+ Tether- VCC U2 FathomX

File: BlueROV2.sch Sheet: / Blue Robotics

Id: 1/1 Title: Blue ROV2 Connections

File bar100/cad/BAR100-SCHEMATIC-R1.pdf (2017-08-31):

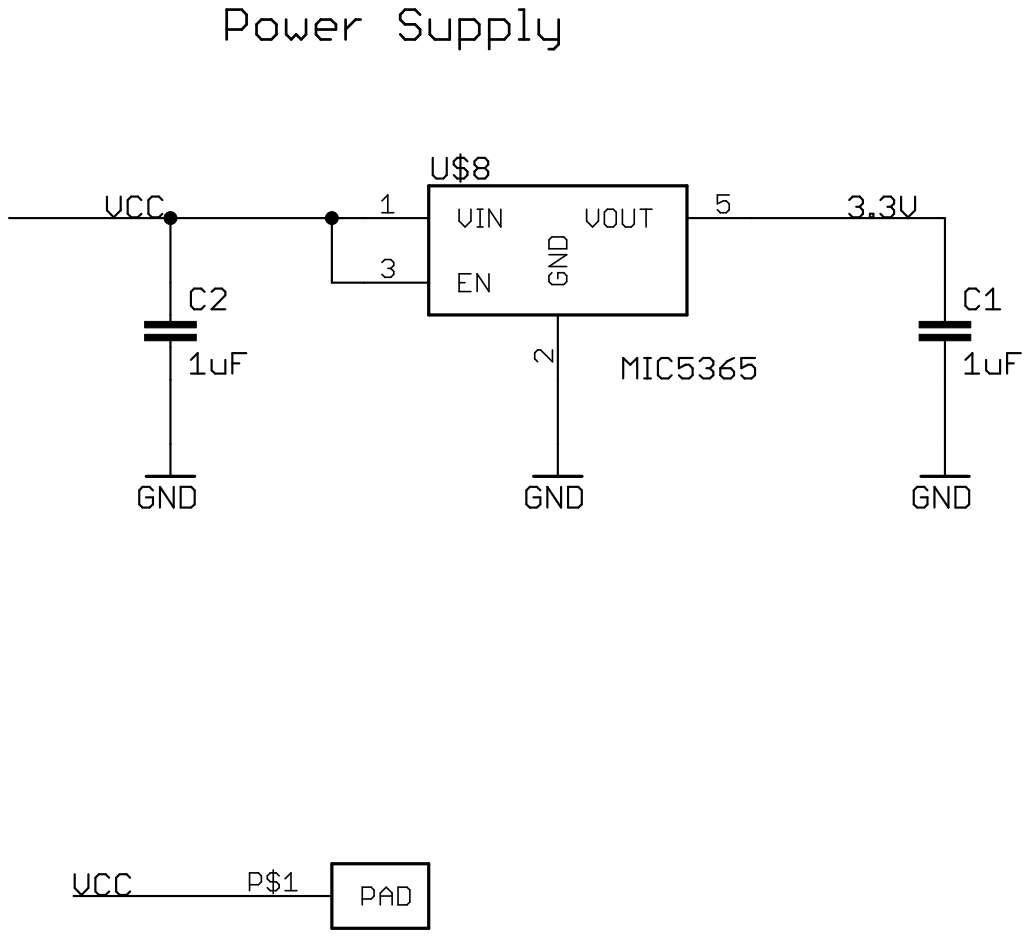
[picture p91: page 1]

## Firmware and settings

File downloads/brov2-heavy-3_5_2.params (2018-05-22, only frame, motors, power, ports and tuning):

1	1	ATC_ANGLE_BOOST	1	2
1	1	ATC_ANG_LIM_TC	1.000000000000000000	9
1	1	ATC_ANG_PIT_P	6.000000000000000000	9
1	1	ATC_ANG_RLL_P	6.000000000000000000	9
1	1	ATC_ANG_YAW_P	6.000000000000000000	9
1	1	ATC_RATE_FF_ENAB	1	2
1	1	ATC_RAT_PIT_D	0.003599999938160181	9
1	1	ATC_RAT_PIT_FF	0.000000000000000000	9
1	1	ATC_RAT_PIT_FILT	30.000000000000000000	9
1	1	ATC_RAT_PIT_I	0.090000003576278687	9
1	1	ATC_RAT_PIT_IMAX	0.444000005722045898	9
1	1	ATC_RAT_PIT_P	0.135000005364418030	9
1	1	ATC_RAT_RLL_D	0.003599999938160181	9
1	1	ATC_RAT_RLL_FF	0.000000000000000000	9
1	1	ATC_RAT_RLL_FILT	30.000000000000000000	9
1	1	ATC_RAT_RLL_I	0.090000003576278687	9
1	1	ATC_RAT_RLL_IMAX	0.444000005722045898	9
1	1	ATC_RAT_RLL_P	0.135000005364418030	9
1	1	ATC_RAT_YAW_D	0.000000000000000000	9
1	1	ATC_RAT_YAW_FF	0.000000000000000000	9
1	1	ATC_RAT_YAW_FILT	5.000000000000000000	9
1	1	ATC_RAT_YAW_I	0.017999999225139618	9
1	1	ATC_RAT_YAW_IMAX	0.222000002861022949	9
1	1	ATC_RAT_YAW_P	0.180000007152557373	9
1	1	BATT2_AMP_OFFSET	0.000000000000000000	9
1	1	BATT2_AMP_PERVOL	17.000000000000000000	9
1	1	BATT2_CAPACITY	3300	6
1	1	BATT2_CURR_PIN	3	2
1	1	BATT2_MONITOR	0	2
1	1	BATT2_VOLT_MULT	10.100000381469726563	9
1	1	BATT2_VOLT_PIN	2	2
1	1	BATT_AMP_OFFSET	0.000000000000000000	9
1	1	BATT_AMP_PERVOLT	17.000000000000000000	9
1	1	BATT_CAPACITY	18000	6
1	1	BATT_CURR_PIN	3	2
1	1	BATT_MONITOR	4	2
1	1	BATT_VOLT_MULT	10.100000381469726563	9
1	1	BATT_VOLT_PIN	2	2
1	1	FRAME_CONFIG	2	2
1	1	INS_GYRO_FILTER	20	2
1	1	MOT_BAT_CURR_MAX	0.000000000000000000	9
1	1	MOT_BAT_CURR_TC	5.000000000000000000	9
1	1	MOT_BAT_VOLT_MAX	0.000000000000000000	9
1	1	MOT_BAT_VOLT_MIN	0.000000000000000000	9
1	1	MOT_FV_CPLNG_K	1.000000000000000000	9
1	1	MOT_HOVER_LEARN	2	2
1	1	MOT_PWM_MAX	0	4
1	1	MOT_PWM_MIN	0	4
1	1	MOT_PWM_TYPE	0	2
1	1	MOT_SAFE_DISARM	0	2
1	1	MOT_SPIN_ARM	0.100000001490116119	9
1	1	MOT_SPIN_MAX	0.949999988079071045	9
1	1	MOT_SPIN_MIN	0.150000005960464478	9
1	1	MOT_SPOOL_TIME	0.500000000000000000	9
1	1	MOT_THST_EXPO	0.649999976158142090	9
1	1	MOT_THST_HOVER	0.349999994039535522	9
1	1	MOT_YAW_HEADROOM	200	4
1	1	SERIAL0_BAUD	115	6
1	1	SERIAL0_PROTOCOL	1	2
1	1	SERIAL1_BAUD	57	6
1	1	SERIAL1_PROTOCOL	1	2
1	1	SERIAL2_BAUD	57	6
1	1	SERIAL2_PROTOCOL	1	2
1	1	SERIAL3_BAUD	38	6
1	1	SERIAL3_PROTOCOL	5	2
1	1	SERIAL4_BAUD	38	6
1	1	SERIAL4_PROTOCOL	5	2
1	1	SERIAL5_BAUD	57	6
1	1	SERIAL5_PROTOCOL	-1	2
1	1	SERVO1_FUNCTION	33	2
1	1	SERVO1_MAX	1900	4
1	1	SERVO1_MIN	1100	4
1	1	SERVO1_REVERSED	0	2
1	1	SERVO1_TRIM	1500	4
1	1	SERVO2_FUNCTION	34	2
1	1	SERVO2_MAX	1900	4
1	1	SERVO2_MIN	1100	4
1	1	SERVO2_REVERSED	0	2
1	1	SERVO2_TRIM	1500	4
1	1	SERVO3_FUNCTION	35	2
1	1	SERVO3_MAX	1900	4
1	1	SERVO3_MIN	1100	4
1	1	SERVO3_REVERSED	0	2
1	1	SERVO3_TRIM	1500	4
1	1	SERVO4_FUNCTION	36	2
1	1	SERVO4_MAX	1900	4
1	1	SERVO4_MIN	1100	4
1	1	SERVO4_REVERSED	0	2
1	1	SERVO4_TRIM	1500	4
1	1	SERVO5_FUNCTION	37	2
1	1	SERVO5_MAX	1900	4
1	1	SERVO5_MIN	1100	4
1	1	SERVO5_REVERSED	0	2
1	1	SERVO5_TRIM	1500	4
1	1	SERVO6_FUNCTION	38	2
1	1	SERVO6_MAX	1900	4
1	1	SERVO6_MIN	1100	4
1	1	SERVO6_REVERSED	0	2
1	1	SERVO6_TRIM	1500	4
1	1	SERVO7_FUNCTION	39	2
1	1	SERVO7_MAX	1900	4
1	1	SERVO7_MIN	1100	4
1	1	SERVO7_REVERSED	0	2
1	1	SERVO7_TRIM	1500	4
1	1	SERVO8_FUNCTION	40	2
1	1	SERVO8_MAX	1900	4
1	1	SERVO8_MIN	1100	4
1	1	SERVO8_REVERSED	0	2
1	1	SERVO8_TRIM	1500	4
1	1	SERVO9_FUNCTION	59	2
1	1	SERVO9_MAX	1900	4
1	1	SERVO9_MIN	1100	4
1	1	SERVO9_REVERSED	0	2
1	1	SERVO9_TRIM	1500	4

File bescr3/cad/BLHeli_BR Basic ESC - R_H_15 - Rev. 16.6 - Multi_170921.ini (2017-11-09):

[ESC0]
Eep_Name=BR Basic ESC
Eep_ESC_Layout=R_H_15
Eep_ESC_MCU=#BLHELI$EFM8B21#
Eep_ESC_Mode=2
Eep_FW_Main_Revision=16
Eep_FW_Sub_Revision=6
Eep_Layout_Revision=33
Eep_Pgm_Startup_Pwr=9
Eep_Pgm_Direction=4
Eep_Enable_TX_Setup=1
Eep_Pgm_Comm_Timing=3
Eep_Pgm_Ppm_Min_Throttle=28
Eep_Pgm_Ppm_Max_Throttle=228
Eep_Pgm_Beep_Strength=152
Eep_Pgm_Beacon_Strength=80
Eep_Pgm_Beacon_Delay=5
Eep_Pgm_Demag_Comp=1
Eep_Pgm_Ppm_Center_Throttle=128
Eep_Pgm_Temp_Prot_Enable=7
Eep_Pgm_Enable_Power_Prot=0
Eep_Pgm_Brake_On_Stop=0
Eep_Pgm_LED_Control=0

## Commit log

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2015-10-30 Updated T100 drawing, added drawings for all thruster and ESC configurations, updated long term test results.
2015-10-31 Added cutaway view of cable penetrator, added cutawywy penetrator imagers.
2015-10-31 Added Blue ESC and Basic ESC diagrams, clarified instructions.
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2015-11-13 Fixed typo in battery page.
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2015-12-27 Added tips to avoid ESC overheating.
2016-01-05 Added inductance and resistance to the motor characteristics.
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2016-01-21 Change pressure and temperature sensor to new schematic, add df-13, and add images for bar30 and celsius for website docs page
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2016-02-02 cable stripping fix
2016-02-19 added lumen folder along with drawings and schematics
2016-02-22 fixed mount drawing
2016-02-22 Added steps for daisy chain and title picture
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2016-02-23 fixed Lumen Assembly 3D models and cleaned up some grammar and formatting
2016-02-23 Added step 4 for the mounting using Lumen Mount instructions
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2016-04-05 cropped a picture and edited daisy chain instructions
2016-04-22 Renamed basic esc files.
    [BESC30-R1.igs, BESC30-R1.sldprt, BESC30-R1.step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]
2016-04-26 Added stl files
    [CAMTILT-RASBPI-MOUNT-X1A.STL, CAMTILT-SERVO-MOUNT-X2A.STL, CAMTILT-STANDOFF-X2B.STL]
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2016-06-08 populated specs pages and added pics to assembly page
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2016-06-08 fixed broken picture links in assembly
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2016-06-09 added note about battery swap time
2016-06-09 removed battery installation section and added reference to the operation manual at the end
2016-06-13 fixed some side bar links and added some wiring diagrams
2016-06-15 added cad diagrams of some steps and formatted some pictures
2016-06-20 cleaned up assembly page for publication and fixed links in specifications page
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2016-07-16 big update to brov2 assembly documentation, added a bunch of pictures and edited the documentation
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2016-07-22 Fix motor numbering typo.
2016-07-27 added note about directionality of the electronics enclosure when installed.
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2016-07-27 edited the frame assembly steps to make directions of the panels more clear
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2016-08-10 added section in assembly manual for power wire strain relief
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2016-08-12 fixed 14 hole endcap cad link
2016-08-12 actually fixed 14 hole end cap cad link
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2016-08-25 added details to battery and vacuum also fixed some formatting and grammar
2016-09-07 updated 2d and 3d drawing files, updated store and product links, modified assembly instructions, and removed examples
2016-09-08 updated camtilt 2d and 3d files to current versions
    [CAMTILT-RASBPI-MOUNT-X1A.STL, CAMTILT-SERVO-MOUNT-X2A.STL, CAMTILT-STANDOFF-X2B.STL]
2016-09-15 added picture for the assembly instructions and modified the introduction
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2016-10-14 camera doc fixes
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2016-10-26 Commit including images and zip files for switch documentation.
    [SWITCH-M-BOLT-10-25-A-R1.IGS, SWITCH-M-BOLT-10-25-A-R1.SLDPRT, SWITCH-M-BOLT-10-25-A-R1.STEP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]
2016-10-26 Moved Switch under electronics category in product manuals page.
2016-10-26 Added links to software setup to assembly and specification page for bluerov2
2016-10-26 Fixed 2D drawing on Switch documentation, png vs PNG file extension broken by windows.
2016-10-26 Fixed store link for Switch.
2016-10-27 added topside wiring to assembly added dive modes and button setup to operation
2016-10-27 Fixed all known build errors and added missing files.
    [SWITCH-M-BOLT-10-25-A-R1.IGS, SWITCH-M-BOLT-10-25-A-R1.SLDPRT, SWITCH-M-BOLT-10-25-A-R1.STEP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]
2016-11-02 added note about driver unstability and reordered to keep joystick stuff together in software-setup
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2016-11-08 Added Payload Skid documentation and updated WTE documentation with clamp drawings and models.
    [SWITCH-M-BOLT-10-25-A-R1.SLDPRT, SWITCH-M-BOLT-10-25-A-R1.STEP, SWITCH-M-DIAL-10-A-R1.IGS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]
2016-11-10 added instructions for fixing motor directions
2016-11-14 fixed motor wiring on starboard diagram
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2016-11-16 fixed broken cad links
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2016-11-18 Added SOS and level converter documentation, modified brov2 assembly documnetation.
2016-11-21 Modified pyalod skid, switch documentation, edited and reordered level converter and sos documentation.
2016-11-23 added link to raspberry pi camera installation instructions
2016-12-20 Fix pressure/depth
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2016-12-24 fixed sboard side motor wire picture
2017-01-12 added 3D cad files for WTE6 and some of the drawings
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2017-02-07 Updated battery recommendation, added charger recommendation to BROV2 kit assembly.
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2017-02-17 still working on big update to advanced electronics assembly
2017-02-21 Fix battery js link.
2017-02-21 Fix battery link.
2017-02-27 edited some pictures and text for lumen power wires
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2017-03-13 corrected M5 screw length
2017-03-14 added links to SOS and CCW thrusters in the new instructions
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2017-03-21 fixed thruster propeller direction inconsistency
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2017-03-22 Added charger link back into kit assembly, back in stock.
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2017-05-10 fixed broken Basic ESC link
2017-05-17 Fixed thruster name typo.
2017-05-23 Added note not to pick up by battery leads.
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2017-06-16 Correct tilt up/down joystic buttons on diagram
2017-06-16 Remove note about unstable 360 mac driver
2017-06-26 updated battery charger recommendation to the one that we sell
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2017-09-07 Fixed new camera file label and link
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2017-09-21 fixed math mistake in thruster mounting locations
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2017-11-08 Added new BasicESC R3 documentation.
    [BESC-R30.IGS, BESC30-R3.SLDPRT, BESC30-R3.STEP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]
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2017-11-10 Fixed Basic ESC name spacing to be consistent.
2017-11-29 added 6in 15 hole end cap, 8in 15 and 25 hole end caps
2017-12-06 fixed broken CAD links on BESC R3
    [BESC30-R3.IGS]
2017-12-06 fixed CAD links for real hopefully
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2018-01-04 Fixed CAD links by capitalizing.
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2018-02-02 Fix print view.
2018-02-13 fixed 3 inch enclosure flange inner diameter
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2018-03-01 Fix brov2 heavy param file
    [brov2-heavy-3_5_2.params]
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2018-04-06 Added note and specifications of thermistor to battery page, changed store page link to R2 battery.
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2018-04-24 Fixed example code compile error
    Line setting sensor model was missing semicolon.
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2018-05-09 Fixed bag labeling for battery enclosure
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2018-06-07 Configure Motor directions: fixed
2018-06-07 linking to internal hash #thruster-guards that does not exist: fixed
2018-06-07 internally linking to /models/PENETRATOR-M-NUT-10-A-R2.zip, which does not exist: fixed
2018-06-07 Internal link error for motors/index.html file: fixed
2018-06-07 Internal link error for motors/m200/index.html: fixed
2018-06-07 internally linking to /cad/WTE4-P-END-CAP-R1.zip, which does not exist: fixed
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2018-08-07 Temporarily removed spool 3D models, too large to upload.
    [MISC-ELEC-BINDER-770-PLUG-L-R1.STP, MISC-ELEC-BINDER-770-PLUG-S-R1.STP]
2018-08-07 downloads: add heavy param file
    [brov2-heavy-3_5_2.params]
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2018-08-15 BROV2 Assembly: Fix PSM link
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2018-08-23 Level-Converter: Fix /cad/ path
2018-08-31 wteclip: initial commit
    Issues with previous wteclip branch led to it being deleted. Relevant files were saved and then re-uploaded to this branch
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2018-09-21 Fix cable repair links.
2018-09-30 Update Binder 770 connector to new documentation format.
    [MISC-ELEC-BINDER-770-PLUG-L-R1.STP, MISC-ELEC-BINDER-770-PLUG-S-R1.STP]
2018-10-03 Updated Thrust Numbers
    Reduced thrust estimates, old numbers were very out of date and predated actual vehicle.
    See here: https://discuss.bluerobotics.com/t/faulty-current-value-reported-by-qgc/3436/3
    Will need to run tests to confirm in the future.
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2018-10-10 m200/sos-doc-updates: Removed specifications and cad .zips
    [M200-MOTOR-R1.SLDPRT, M200-MOTOR-R1.STEP, M200-MOTOR-R1.STL]
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2018-10-10 switch-updates: updated documentation and removed cad files
    [SWITCH-M-BOLT-10-25-A-R1.IGS, SWITCH-M-BOLT-10-25-A-R1.STL]
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2018-10-24 m100-updates: Updated docs and removed cad files
    [M100-MOTOR-R1.IGS, M100-MOTOR-R1.SLDPRT, M100-MOTOR-R1.STEP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]
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2018-12-05 Brov2: fix sensors link
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2018-12-15 Revert "Battery page update"
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2019-04-11 sos-leak-sensor: redirect to new docs
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2019-09-25 Removed Spaces From Thrust Power Legend Labels
    For better spacing at full resolution on web page.
2020-04-22 Redirect pressure-depth now that the page is fixed
2020-11-23 power-sense-module.md: remove redirect
    We don't have data for the power-sense-module r1 available elsewhere, so this page should be accessible.
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2023-03-05 Fix broken link
    It looks like the ArduPilot downloads page has moved. In any case, the current link is malformed.
